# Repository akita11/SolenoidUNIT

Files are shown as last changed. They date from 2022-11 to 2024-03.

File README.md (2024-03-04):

# SolenoidUNIT

ソレノイドやDCモータなどの負荷を、Grove端子から最大2個まで制御できます。負荷と電源の接続コネクタの違いで2種類あります。

## SolenoidUNIT

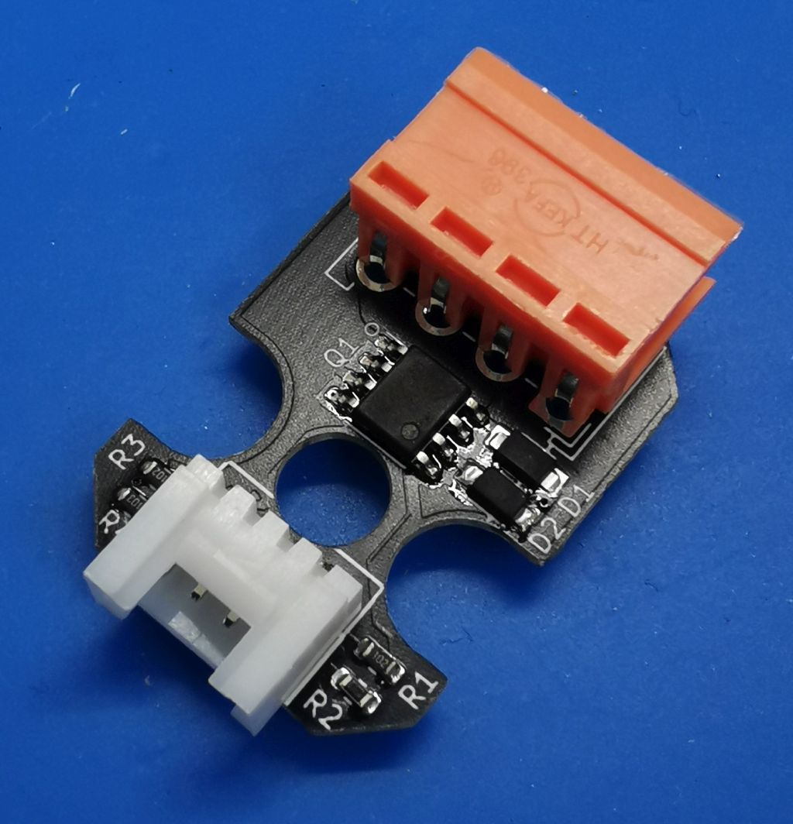
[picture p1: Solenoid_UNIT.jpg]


オレンジ色のコネクタ(VH3.96-4p)に、負荷用の電源と負荷を接続します。M5Stackの[BAVGソケット](https://www.switch-science.com/products/7234)を使うと、電源は2.1mmプラグ、負荷はスプリング端子で接続できて便利です。

負荷の電源はオレンジ色のVH3.96コネクタ、またはGrove端子のVDDから選択できます。Grove端子のVDDへの電源供給能力が不足する場合は[TypeC2Grove UNIT](https://www.switch-science.com/products/8453)等を使用してください。

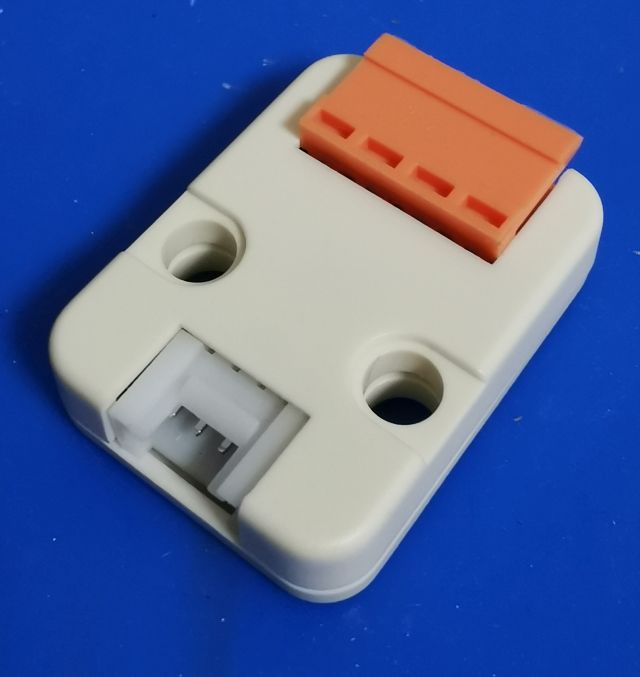
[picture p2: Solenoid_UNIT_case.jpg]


基板形状が「[M5Stack用VH3.96-4ピンユニット[U020]](https://www.switch-science.com/products/4055)」と同一のため、そのケースを使うことができます。

### 使い方

ソレノイドとの接続は、電源供給方法に応じて以下の2通りがあります。制御方法は後述します。

#### ACアダプタ等から供給する場合

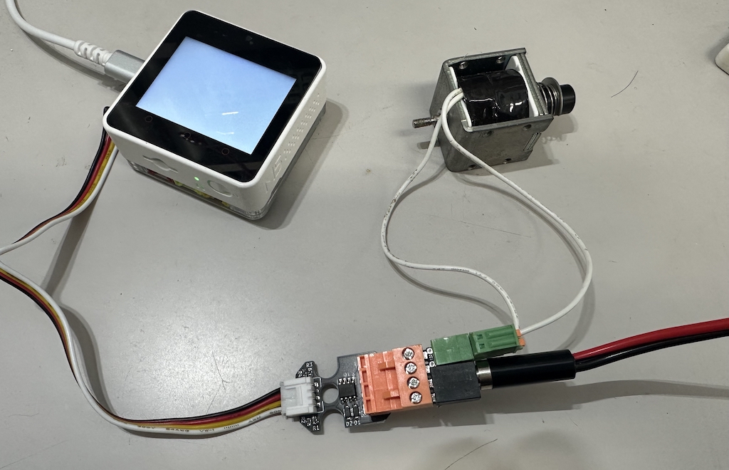
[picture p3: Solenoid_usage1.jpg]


ソレノイドの定格電圧が12V等の5Vよりも高い電圧の場合は、ACアダプタ等をオレンジ色コネクタのVS-G間、ソレノイドをA+とA-Bの間に接続します。（M5Stackの[BAVGソケット](https://www.switch-science.com/products/7234)を使うと、電源は2.1mmプラグ、負荷はスプリング端子で接続できて便利です）

#### Grove端子から供給する場合

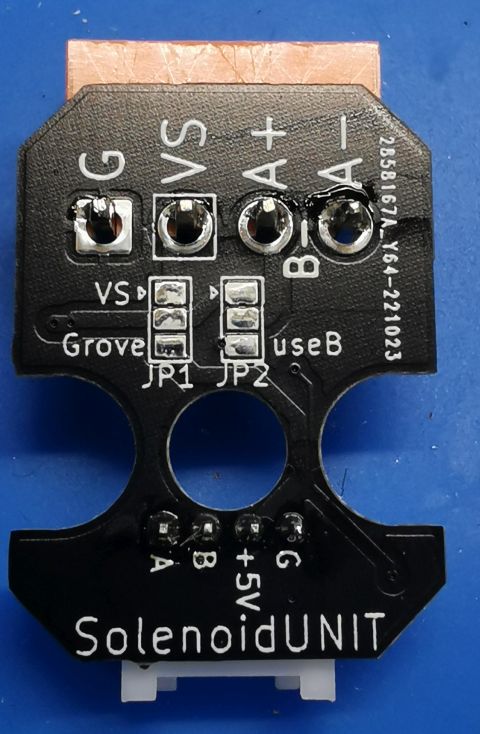
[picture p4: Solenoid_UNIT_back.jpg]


一般のソレノイドは5Vでは駆動できませんが、5Vで駆動する場合は、電源をGrove端子から供給することができます。
裏面のJP1の、中央-VS(上側)の端子がつながっていますので、カッター等でカットし、中央と反対側の"Grove5V"側を、ハンダを盛るなどしてショートします。これによって、負荷への電源がGrove側の+5Vから供給されます。
ただし、一般にソレノイドは消費電流が多く、マイコン側の+5V電源の供給能力が不足する場合がほとんどです。そのような場合は、[TypeC2Grove UNIT](https://www.switch-science.com/products/8453)を使用して、負荷側の電源をUSB Type-C端子から供給することができます。別途USB-CコネクタのACアダプタ等を接続してください。

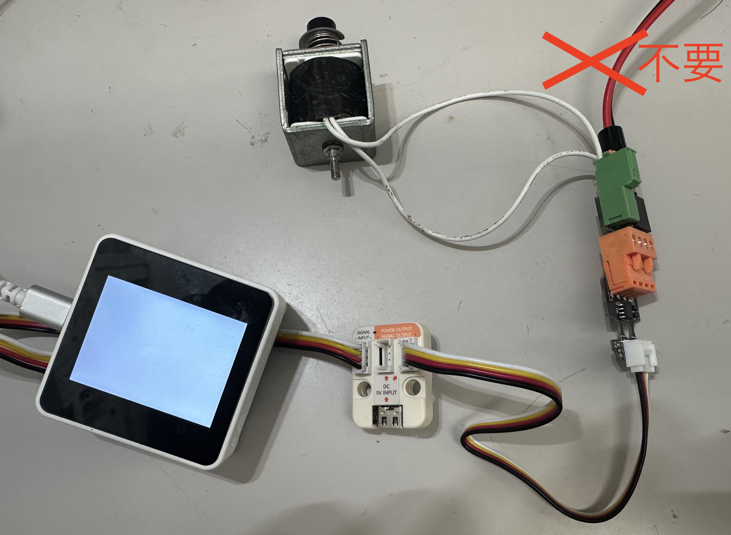
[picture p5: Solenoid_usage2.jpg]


#### 2個のソレノイドを制御する場合

必要に応じて、2個のソレノイドを制御することができます。ただし接続がやや複雑ですので、ご注意ください。

- JP2 : VH3.96コネクタの2番ピンの割り当て。「負荷Aのプラス側」（デフォルト）または「負荷Bのマイナス側」。
  - 「負荷Aのプラス側」（デフォルト）の場合（下図(a)）：負荷Aを1番ピン（マイナス側）と2番ピン（プラス側）に接続。負荷は1個のみ(Groveの1番ピンで制御）
  - 「負荷Bのマイナス側の場合」（下図(b)）：負荷A, Bのプラス側はVDD（3番ピン）に接続し、負荷A, Bのマイナス側をそれぞれ1番ピンと2番ピンに接続。負荷は2個（Groveの1番ピン（負荷A）と2番ピン（負荷B）で制御）

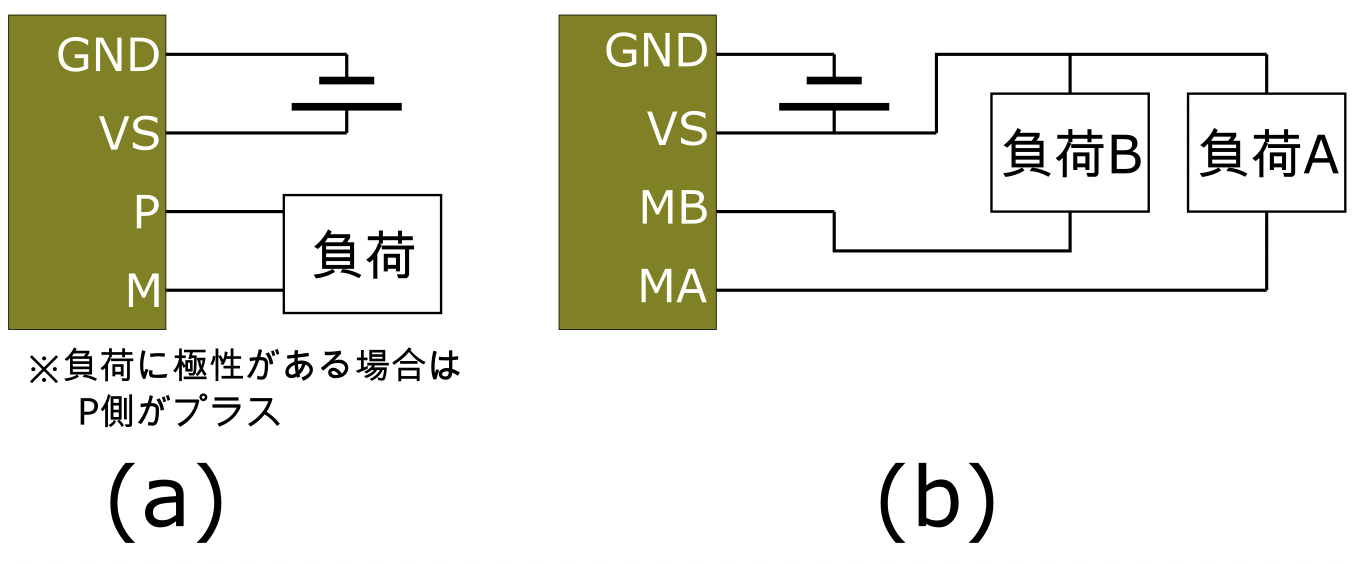
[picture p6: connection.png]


## Solenoid5V_UNIT

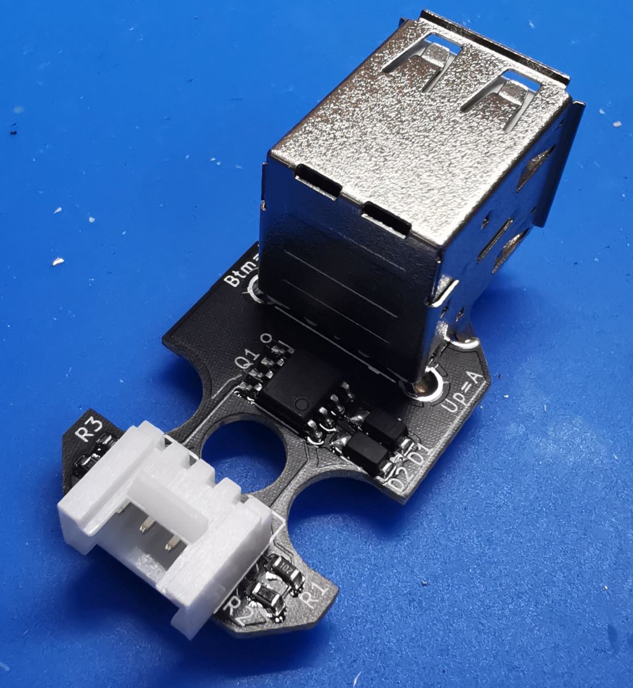
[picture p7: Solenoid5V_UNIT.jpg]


[タカハの5Vソレノイド](https://www.takaha.co.jp/co/ss/)を接続して制御できます。

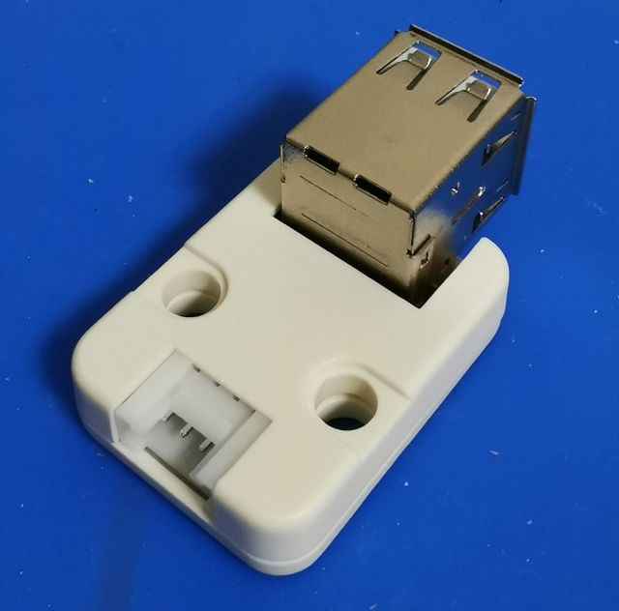
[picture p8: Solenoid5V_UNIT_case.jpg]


基板形状が「[M5Stack用VH3.96-4ピンユニット[U020]](https://www.switch-science.com/products/4055)」と同一のため、そのケースを使うことができます。

2段USBコネクタの上側がソレノイドA（Groveの1番ピンで制御）、下側がソレノイドB（Grovの2番ピンで制御）です。

マイコン（M5Stack等）との接続は以下のように行います。

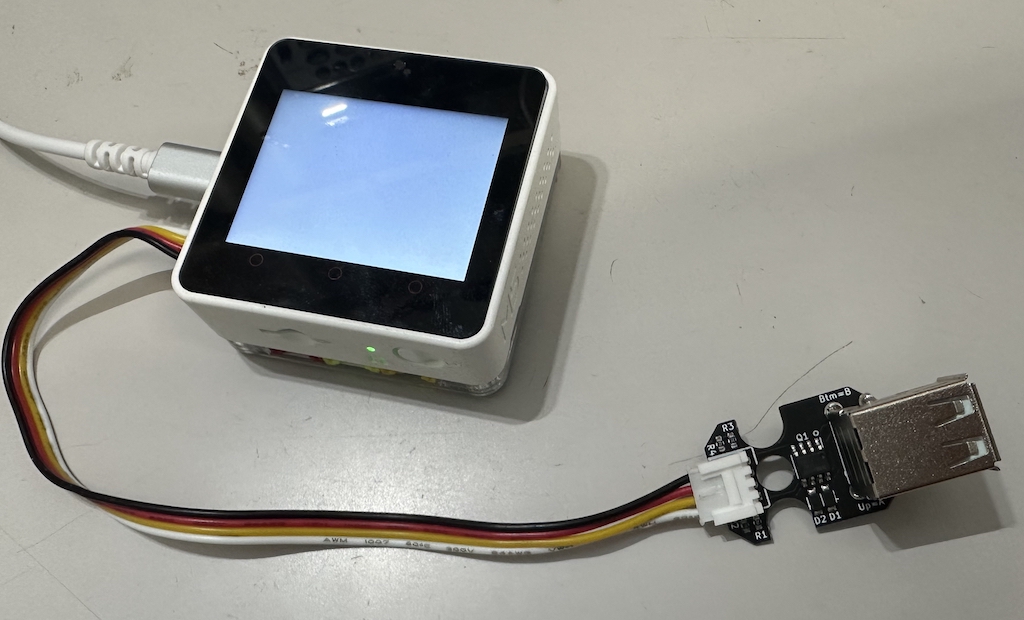
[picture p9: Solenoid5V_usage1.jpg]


ただしソレノイドは通電時の消費電流が大きいため、マイコン側の電源供給能力が不足する場合があります。その場合は、[TypeC2Grove UNIT](https://www.switch-science.com/products/8453)を使用して以下のように接続してください。負荷側の電源はUSB Type-C端子から供給することができます。別途USB-CコネクタのACアダプタ等を接続してください。

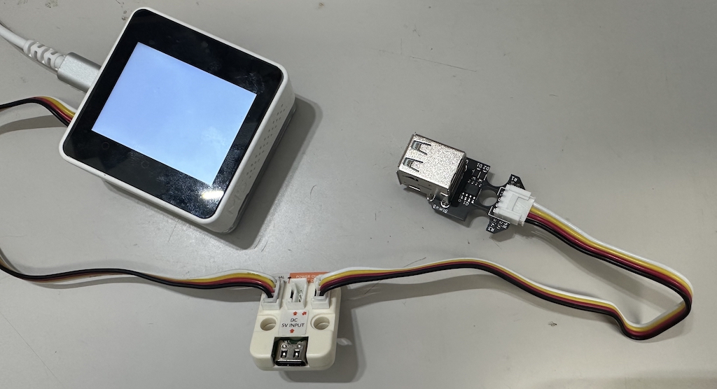
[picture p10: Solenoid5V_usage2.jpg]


## マイコン(M5Stack等)からの制御

ソレノイドのの制御は、Grove端子の2本の信号（A/B/VDD/GNDの順）で行います。AまたはBに"1"を与えると負荷がONとなり、"0"でOFFとなります。SolenoidUnitの標準接続（ソレノイド1個）ではA端子のみを使います。

UIFlowでの[使用例](Solenoid5V_test.m5f)（以下）を参考にしてください。（Core2のPortAに接続した場合。A=GPIO32、B=GPIO33）

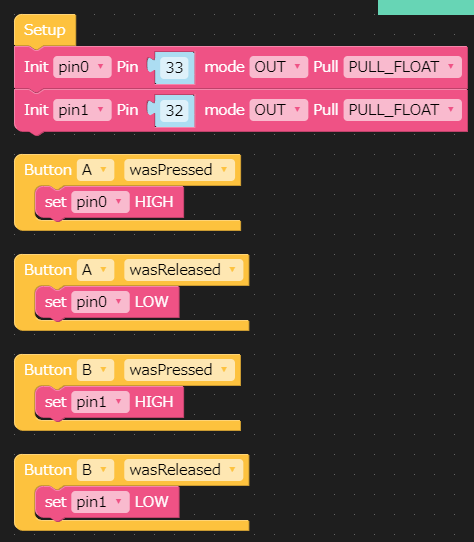
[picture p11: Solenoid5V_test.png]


## Author

Junichi Akita (akita@ifdl.jp, @akita11)

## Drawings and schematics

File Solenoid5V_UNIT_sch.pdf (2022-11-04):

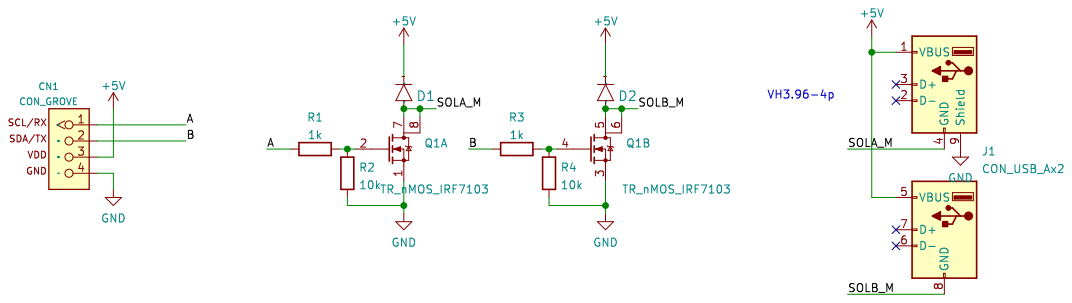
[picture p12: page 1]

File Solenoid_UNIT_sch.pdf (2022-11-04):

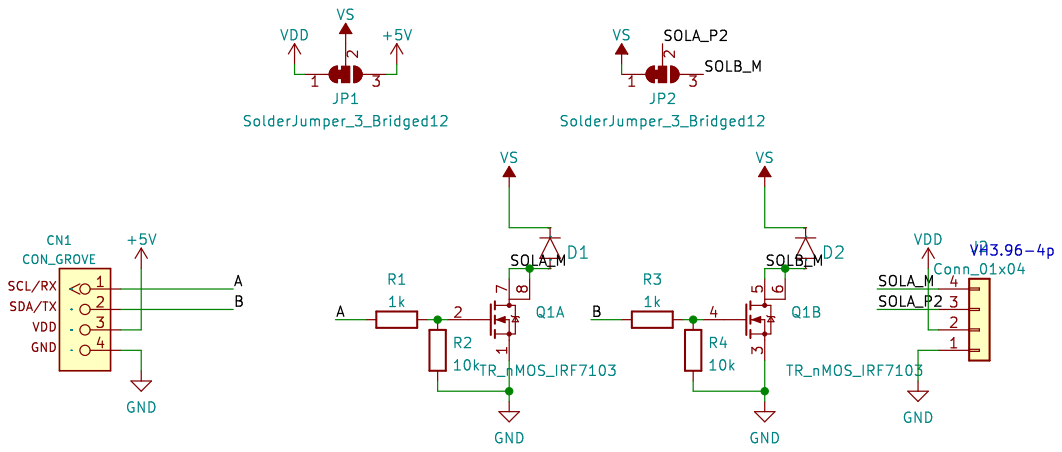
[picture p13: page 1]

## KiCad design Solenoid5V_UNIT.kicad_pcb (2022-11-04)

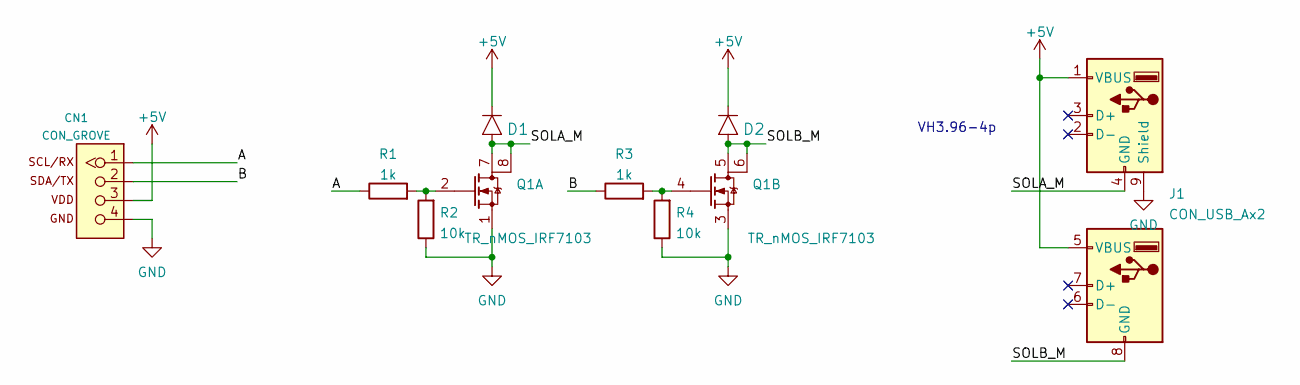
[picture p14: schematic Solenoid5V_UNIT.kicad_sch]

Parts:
CN1: CON_GROVE; CON_GROVE_H
D1, D2: DIODE; D_SOD123FL
J1: CON_USB_Ax2; USB_A_Wuerth_61400826021_Horizontal_Stacked
Q1: TR_nMOS_IRF7103; SO-8_3.9x4.9mm_P1.27mm
R1, R3: 1k; R_0603_1608Metric
R2, R4: 10k; R_0603_1608Metric

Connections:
+5V: CN1.3, D1.K, D2.K, J1.1 (VBUS), J1.5 (VBUS)
/A: CN1.1, R1.1
/B: CN1.2, R3.1
/SOLA_M: D1.A, J1.4 (GND), Q1.7 (D), Q1.8 (D2)
/SOLB_M: D2.A, J1.8 (GND), Q1.5 (D), Q1.6 (D2)
GND: CN1.4, J1.9 (Shield), Q1.1 (S), Q1.3 (S), R2.1, R4.1
unnamed: Q1.2 (G), R1.2, R2.2
unnamed: Q1.4 (G), R3.2, R4.2

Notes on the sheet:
VH3.96-4p

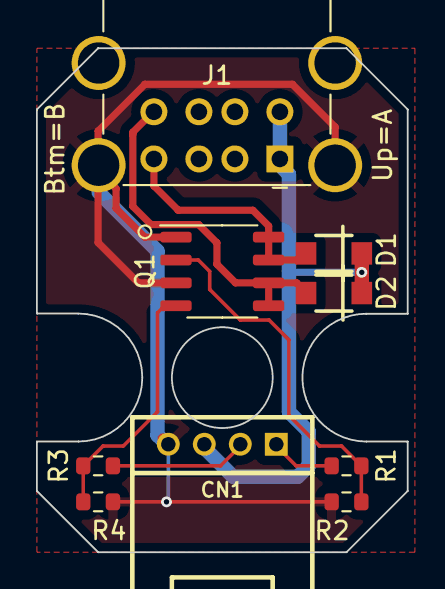
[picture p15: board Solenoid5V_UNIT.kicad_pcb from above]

Board: 2 copper layers, 20.6 x 28.0 mm, 9 parts (0 on the bottom side), 8 nets.

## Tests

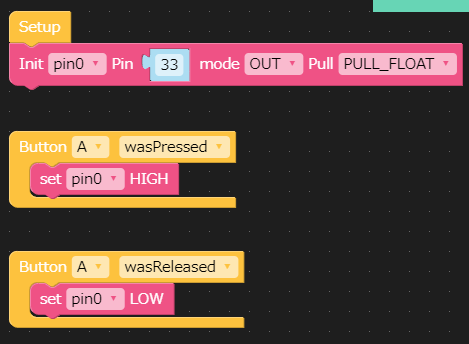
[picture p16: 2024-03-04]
Solenoid_test.png
